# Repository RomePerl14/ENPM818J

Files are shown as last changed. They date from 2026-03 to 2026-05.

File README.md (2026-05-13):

# FINAL PROJECT OVERVIEW

For my final project submission, I used a PD controller and an ESP32 to control a brushless DC motor. This README contains the hardware used by the system, the system electronics and wiring, and the software to drive the system. By the end of this README, you should build and replicate the results exaclty from this final project! At least, that is my hope with this README :)

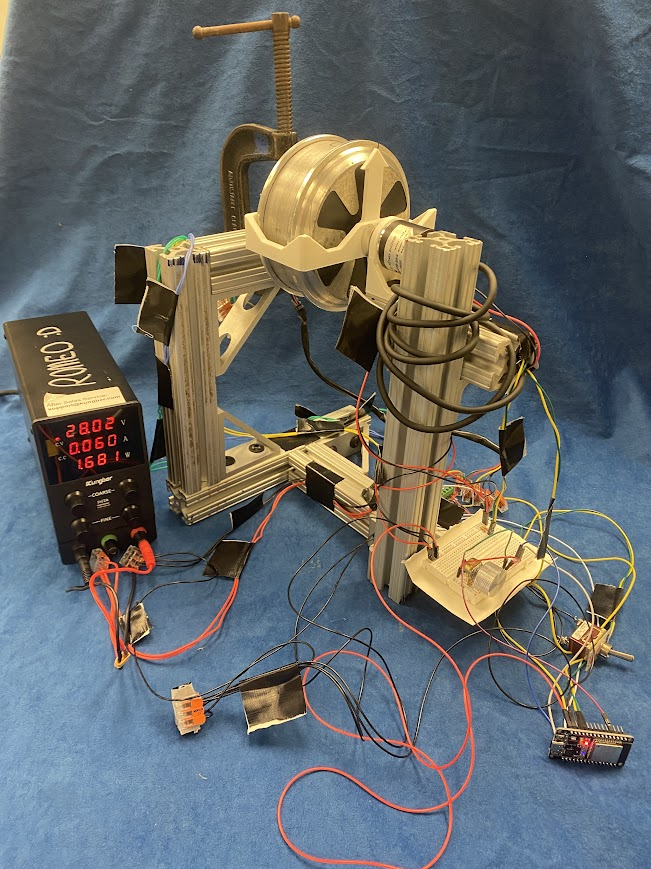
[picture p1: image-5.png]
 

## VIDEOS (click on images)
### ALL ENCOMPASSING VIDEO (I spliced everything into one video)
WATCH ME! (https://www.youtube.com/watch?v=Hu35tKas5SA)
### FINAL PRESENTATION VIDEO
IMAGE ALT TEXT HERE (https://www.youtube.com/watch?v=4x_1EzVbeUM)
### CODE OVERVIEW VIDEO
IMAGE ALT TEXT HERE (https://www.youtube.com/watch?v=HJQnwBiKr0g)
### CODE OVERVIEW WITH SYSTEM DEMO
IMAGE ALT TEXT HERE (https://www.youtube.com/watch?v=exr8jvf5Yu8)
### SYSTEM DEMO
IMAGE ALT TEXT HERE (https://www.youtube.com/watch?v=Gk0GASkIG9Y)

## Tools Needed:
- Wire strippers
- Dupont wire crimper
- Dupont wire connectors, or Arduino jumper wires (a LOT, see wiring diagram)
- Soldering tool
- Solder
- [1] large C-clamp
- 3/16 allen wrench (I think)

## Hardware Requirements
- [1] ESP32-WROOM-32: https://a.co/d/05TtJUjU
- [1] USB-C data cable
- [1] Hoverboard Motor: https://a.co/d/0681CQAJ (DO NOT BUY THIS - this is just an example of the motor. Any 3-Phase, 120 degree out-of-phase motor with an included hall effect sensor *should* work)
- [1] RioRand 350W 6-60V 3-Phase PWM DC Brushless Motor Speed Controller with Hall Sensor: https://a.co/d/0fNlEnNE
- [1] Any 28V (or more) power supply will work, measured no-load power was ~10 Watts 
- [n] 1515 8020 aluminum extrusion (see attached CAD for exact details and dimensions, though these are not hard requirements)
- [3] 15 series 8020 Tall Gusseted Inside Corner Bracket: https://8020.net/4336.html
- [3] 15 series 8020 Lite Transition Inside Corner Bracket: https://8020.net/4509.html
- [20] 15 series 8020 Bolt Assembly: https://8020.net/3320.html
- [1] Breadboard or equivalent way of connecting circuitry together (see circuit diagram below, or here [TODO - attach link])
- [1] One-turn analog potentiometer
- [2] 2.2k Ohm resistors
- [1] basic on/off switch
- [20] WAGO Lever-Nuts 3-Conductors varient (or more, less probably won't work without being annoying): https://a.co/d/0gCFwZCQ
- [1] Taiss/Incremental Rotary Quadrature Encoder, 600P/R: https://a.co/d/0cLU70xH
- 3D printer or ability to 3D print 3 components
- [1] goBilda 1309 Series Sonic Hub (6mm D-Bore): https://www.gobilda.com/1309-series-sonic-hub-6mm-d-bore/
- [3] M3 x 8mm
- [4] M4 x 20mm
- [2] M4 x 12mm

## Software Requirements
- ESP-IDF v2.1.0 (I used the VScode plugin and followed instructions on getting it working directly from Espressif): https://docs.espressif.com/projects/esp-idf/en/stable/esp32/get-started/index.html
- Visual Studio Code
- Windows 11 (?)

## Software Configuration
In your project configuration, specifically in ```sdkconfig```, you must change the following parameters:

```CONFIG_FREERTOS_HZ=100```

Change this too:

```CONFIG_FREERTOS_HZ=1000```

# SETTING UP THE HARDWARE
## Step 1: print the hardware
The system relies on three 3D prints to connect the motor and the encoder. The motor doesn't have any traditional mounting holes since it was original designed to spin a tire really fast, and the tire was built into the rotor. As such, we need to print an adapter to allow us to connect the motor and the encoder. We also need to print a mount for the encoder.

### MOTOR SIDE PRINTS
The two prints that are attached to the motor are the armature and direction arrow. You can find them here [TODO - ADD LINK]

<u>**Motor-To-Encoder Armatrure:**</u>

<img src="image-2.png" width="400"/> 

<img src="image-3.png" width="400"/> 

<u>**Direction Indicator Arm:**</u>

<img src="image-4.png" width="200"/> 

### ENCODER SIDE PRINTS
The only print needed for the encoder is it's mount, which you can find [here](FinalProj/STL/)

<u>**Encoder Mount:**</u>

<img src="image.png" width="300"/> 
<img src="image-1.png" width="300"/>

### 8020 MOTOR MOUNT
Because this is a little complex and also not necessarily required (another mounting method can be designed), see the CAD for more detail [TODO - ADD LINK]

[TODO - ADD PICTURES OF THE CAD]

# SETTING UP THE ELECTRONICS
Below is an electrical schematic of the system. You can utilize the WAGO connectors for most connections, however you will need jumper wires for connecting to the ESP32 and other peripherals. The general implementation is up to interpretation, however the exact wiring of the system used for this project is reflected in the wiring diagram!

[TODO -ADD PICTURE OF WIRING DIAGRAM]

# SETTING UP THE SOFTWARE
After installing Visual Studio Code, ESP-IDF, and the VSCode ESP-IDF extension, you can then clone this repository, or whatever means you want to get the ESP32 project code onto your own machine. Once it's on your machine and your project is configured, you should be able to build, flash, and monitor the code out-of-the-box! There are no external libraries utilized, just ESP32 libraries, C libraries, and FreeRTOS libraries (which should be downloaded with ESP-IDF).

## Software Overview
You will find all the code to run this project in one simply file: *`the_main_thingy.c`*. This File is located in the FinalProj/rotary_encoder/main/ folder. It's CMakeList.txt file (generated by ESP-IDF) is also in that file

There are three main tasks being run by the ESP32:
- The control task, running at 1000 Hz on CORE 1
    
- The potentiometer task, running at 100 Hz on CORE 0
    - Running it at 100 Hz allows the potentiometer to be sampled rather quickly and enable good tracking of the system
- The display task, running at 10 Hz on CORE 0
    - Because this is not a critical task, we run at an O.K. speed

### The Control Loop Task [```position_pid_task()```]
This task runs the PD control loop, and thats it! It reads the encoder counts from the onboard pulse counter, computes the command signal, and then writes a PWM value. The control loop itself is very standard:
- read() [```ctrl_loop_read(int *encoder_counts)```]
    - read the measurements from the incremental encoder, specifically read the output from ```pcnt_unit_get_count()```
- update() [```compute_position_pid_standard(float err, float prev_err, pid_gains gains, float freq)```]
    - Get the user command, and generate the control signal from the PD controller 
    - note that err, prev_err are computed in the task's while loop, not in the above function. pid_gains and frequency should technically be constants
- write() [```ctrl_loop_write(float *U)```]
    - Generate the PWM signal based on the PD controllers output, and write it to the PWM generator using ```ledc_set_duty()``` and ```ledc_update_duty()```

There is an additional update function called ```compute_position_pid_velocity(float err, float vel, pid_gains gains)``` which uses the velocity as a damping factor, rather than the change in error

#### Data Structures
There are two custom data structure implemented to ease function inputs, the ```pid_gains``` struct and the `pid_mode` enumerator. `pid_gains` stores the PID gains for the controller. The members of the struct Kp, Kd, and Ki are set before the beginning of the while loop in the task. `pid_mode` is used to switch between change in error PID or direct velocity PID

#### Interesting Things
To reduce the need to divide, many conversion factors which would require divison are pre-computed before the beginning of the while loop. In addition, rather than deriving the position measurements to get measured velocity using the common formula:

```(p(t) - p(t-1))/dt```

We use:

```(p(t) - p(t-1))*freq```

Since our control frequency is stable (or at least, should be thanks to FreeRTOS), we can say that our delta time is "constant" and 1/dt = 1/period = frequency. Thus, saving us the need to divide in order to get velocity. This is done a lot, where the inverse is computed ahead of time and then multiplied by, in an attempt to *not have to divide.*

We also used ```vTaskDelayUntil()``` rather than ```vTaskDelay()``` since we want our code to mandate a 1kHz frequency. Seemingly, the control loop computation is faster than 1 ms, allowing us to wait until we 1ms has passed before returning

Finally, we also store the the actual position, desired position (or commanded), the encoder counts, the error, and the control signal in global buffers labeled ```ACTUAL_POS```, ```ENCODER_COUNTS```, ```ERROR```, ```CONTROL_SIGNAL``` so that our display task can handle printing to the terminal, rather than the control loop.

We SHOULD filter the velocity signal using a low-pass filter (example from here: https://kiritchatterjee.wordpress.com/2014/11/10/a-simple-digital-low-pass-filter-in-c/) because it's WAY noisy! But I haven't implemented that yet. I should probably filter the potentiometer too!

### The Potentiometer Task [`read_potentiometer_task()`]
This is pretty much stripped directly from their example, as there was no point in fixing a broken clock if it's right twice a day, or something like that! You can find the ESP32 source code here: https://github.com/espressif/esp-idf/tree/v6.0.1/examples/peripherals/adc/continuous_read

### The Display Task [`display_control_data_task()`]
This task is very straight forward. Get the data from the buffers, and then print it to the console!

### PWM Generator
Its important to note that the PWM generator is generating a signal with a frequency of 20kHz. From online research (googling), 20kHz seemed to be a good PWM frequency to ensure good motor control. With this goal in mind, we needed to calculate the control duty resolution (see PWM generator below), and found that our maximum PWM command was 2047 bits, and our resolution was 1 bit, so we have  2047 different possible commands to send to the hardware.

## Final Takeaways
Many of the things implemented for this project were borrowed from other pioneers on the internet. Here are my sources:
- Motor driver wiring information: https://mad-ee.com/easy-inexpensive-hoverboard-motor-controller/
- ESP32 pinouts: https://lastminuteengineers.com/esp32-pinout-reference/
- ESP32-IDF examples (of which I used many): https://github.com/espressif/esp-idf/tree/v6.0.1/examples
    - potentiometer: https://github.com/espressif/esp-idf/tree/v6.0.1/examples/peripherals/adc/continuous_read
    - PWM generator: https://github.com/espressif/esp-idf/tree/v6.0.1/examples/peripherals/ledc/ledc_basic
    - Generic GPIO: https://github.com/espressif/esp-idf/tree/v6.0.1/examples/peripherals/gpio/generic_gpio
    - Encoder counter: https://github.com/espressif/esp-idf/tree/v6.0.1/examples/peripherals/pcnt/rotary_encoder
    - Duty Cycle and Precision calculations: https://documentation.espressif.com/esp32_technical_reference_manual_en.pdf#ledpwm, https://docs.espressif.com/projects/esp-idf/en/v4.3/esp32/api-reference/peripherals/ledc.html
    - PID control loop with a similar device: https://geekeeceebee.com/DCMotor%20Position%20Tracking.html
    - Task creation stuff: https://randomnerdtutorials.com/esp32-dual-core-arduino-ide/

Without the above documentation, this project (which I started on 5/8, and ended on 5/11... my parts didn't come in until 5/6!!) I would have NEVER been able to actually build this system, let alone get it running. But, I've gotten it running, and I'm quite proud of the little scamp. The poorly tuned, aggressive, spaghetti-like scamp. Hopefully if you are reading this, you may also one day be proud of your own little PID testbed, maybe even this very one!

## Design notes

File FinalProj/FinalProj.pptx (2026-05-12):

## Real-Time Position and Velocity Control of a Brushless DC Motor

Romeo Perlstein
ENPM818J Final Project

## Team

Romeo Perlstein:
- Aerospace Engineering Masters Student
- Likes space robots, human spaceflight, and human/robot collaboration in space

## Project Overview

Mission Statement:
Control the position of a hobby-grade brushless DC motor

## Requirements

Mission Level Requirements:
1. Fast control loop to implement basic PD controller
2. Position encoder to track live position of motor
3. Brushless DC motor
4. Brushless DC motor driver

## Requirements

Mission Level Requirements Reasonings:
1. PD controller needs to run at a relatively fast rate for good tracking
2. Need positional sensor readings in order to command position using PD controller
3. Need physical actuator to drive system, brushless DC motors are relatively challenging to work with compared to brushed DC motors and enable a more challenging project
4. Need a drive to convert command signals to phase current cycles (developing a custom one deemed out-of-scope)

## Requirements Cont’d

System Level Requirements:
1. Control loop that can run on the order of ~1kHz
2. Ability to read encoder pulses at frequency of ~10kHz
3. Ability to generate pulse-width-modulated (PWM) signal at frequency of roughly ~20kHz
4. Ability to send digital outputs at a fast rate (~1kHz)
5. Control input circuit (a.k.a potentiometer) for position commands

## Requirements Cont’d

System Level Requirements Reasoning:
1. Position PID control of motors needs to run at frequencies on the order of kHz or faster for stable and smooth control
2. High-resolution encoders generate pulses faster than typical while loops or interrupt service routines can handle
3. High frequency PWM signals enable smooth motor motion
4. Digital output for direction has to change at the same rate of the control loop
5. User input to demonstrate motor control

## Final System

## Final System (labeled)

## Core Components

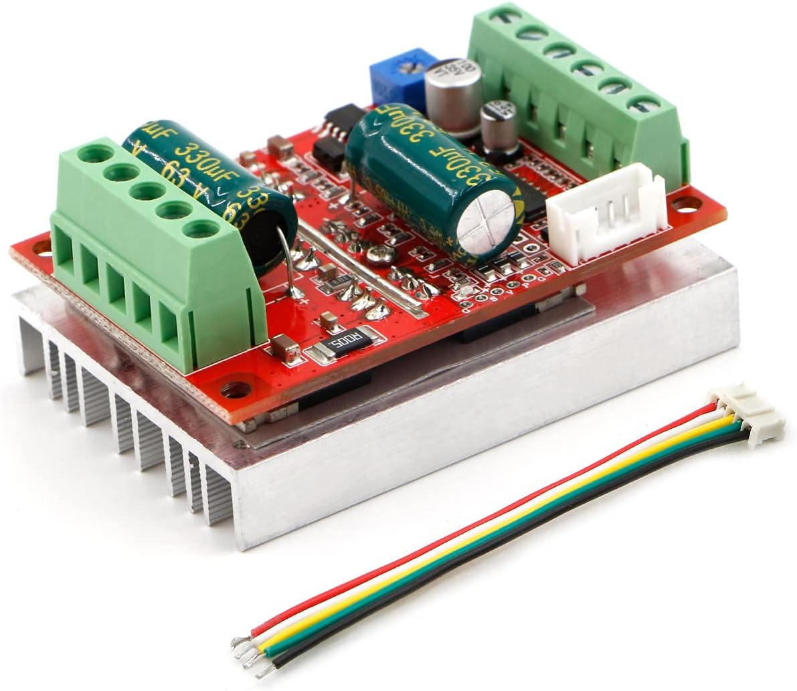
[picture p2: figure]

- RioRand 3-Phase Brushless DC motor driver with PWM input
- Hoverboard motor
- 1515 80/20 extrusion
- ESP32 WROOM
- Quadrature Encoder

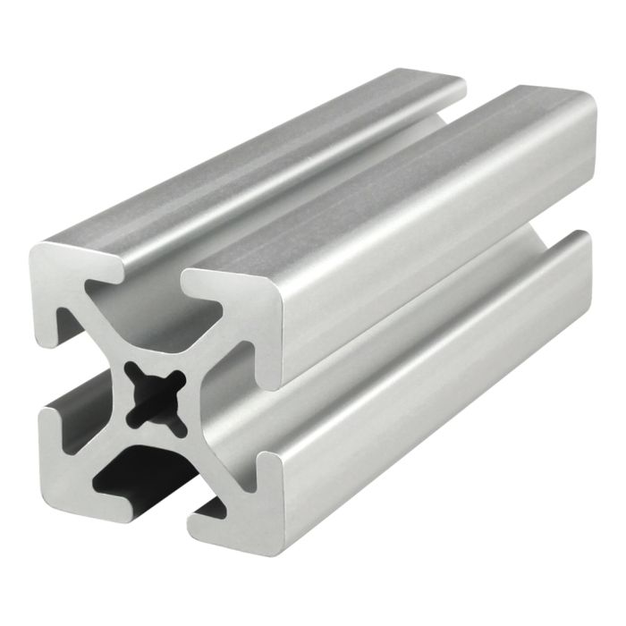
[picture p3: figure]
1515-S | 1.50” X 1.50” Smooth Surface T-Slotted Profile - Four Open T-Slots
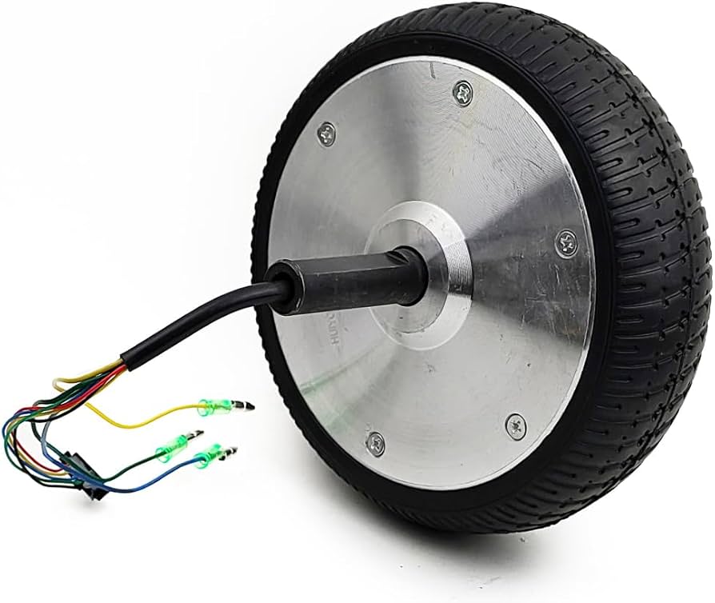
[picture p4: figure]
Amazon.com: 6.5 Inch Self Balancing Scooter Motor Wheel with Tire Self Balance Unicycle Hover Board Motor Replacement : Sports & Outdoors
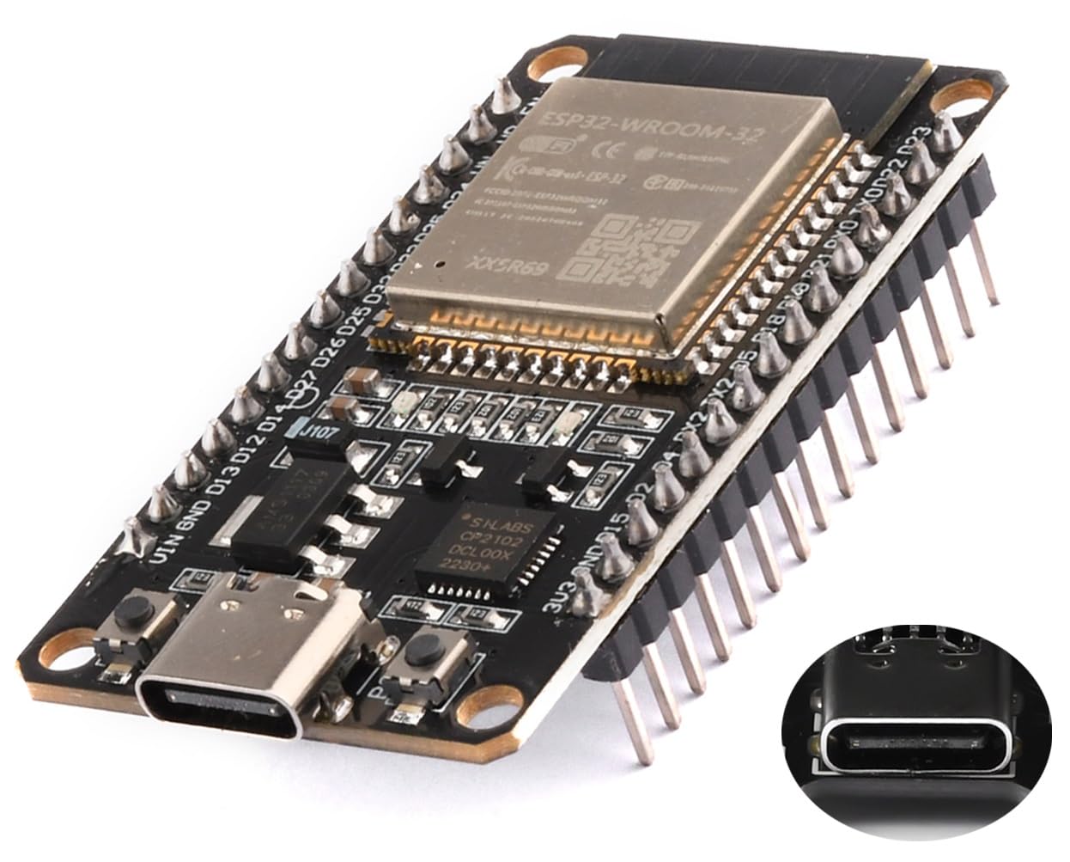
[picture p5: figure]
Amazon.com: ESP32 Type-C Module ESP32 30PIN NodeMCU Development Board ESP32- WROOM-32 2.4 GHz WLAN CP-2102 : Electronics
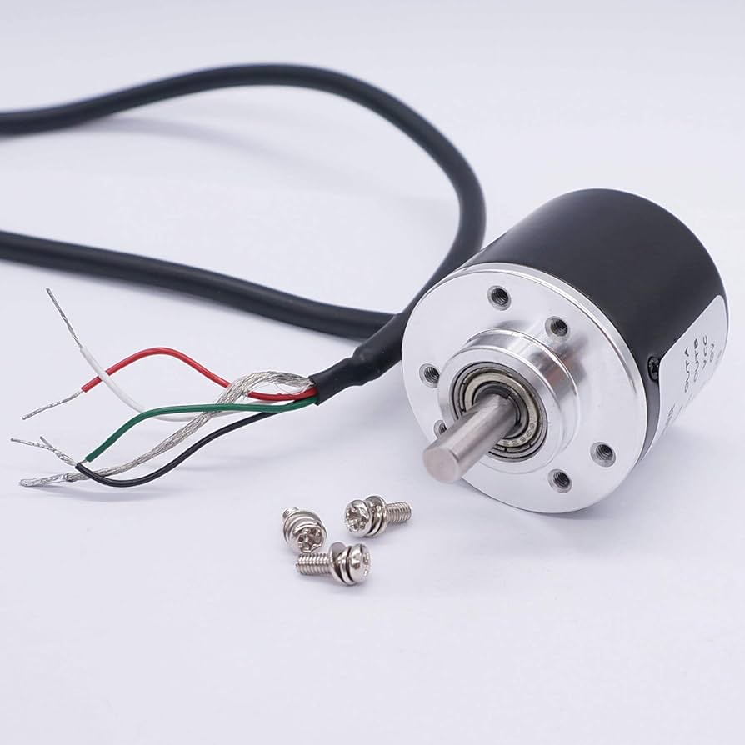
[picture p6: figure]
Amazon.com: Taiss/AB 2 phase Incremental Rotary Encoder 360P/R DC 5-24v Wide Voltage Power Supply 6mm Shaft 360P/R : Industrial & Scientific

## Additional Components

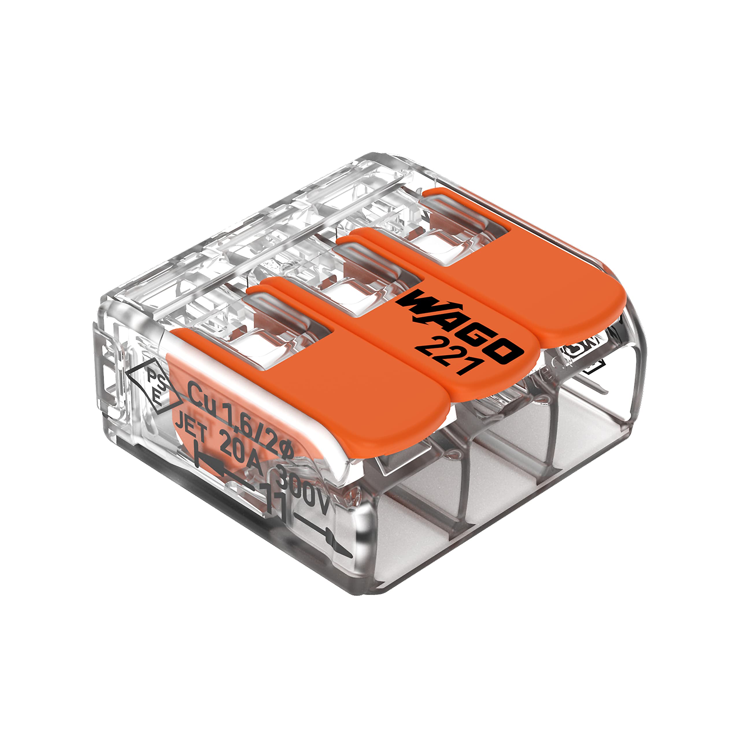
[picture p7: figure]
Amazon.com: 221-413 | WAGO Lever-Nuts® Splicing Connector | for Solid and Stranded Conductors | 3-Conductor with Operating levers | 24-12 AWG | Transparent housing | [Box of 50 Pieces] : Industrial & Scientific

- WAGO lever-lock connectors
- Breadboard
- 30V-10A power supply
- Enable/disable switch
- Potentiometer
- C-clamp

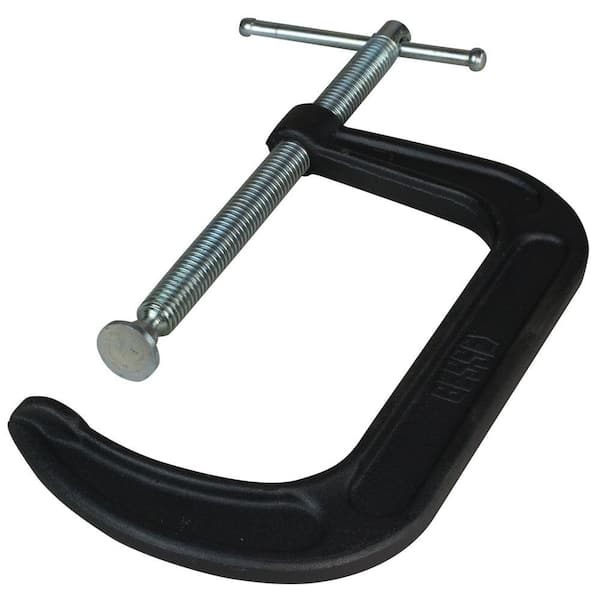
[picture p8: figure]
BESSEY CM Series 6 in. Capacity Drop Forged C-Clamp with 3-1/2 in. Throat Depth CM60 - The Home Depot
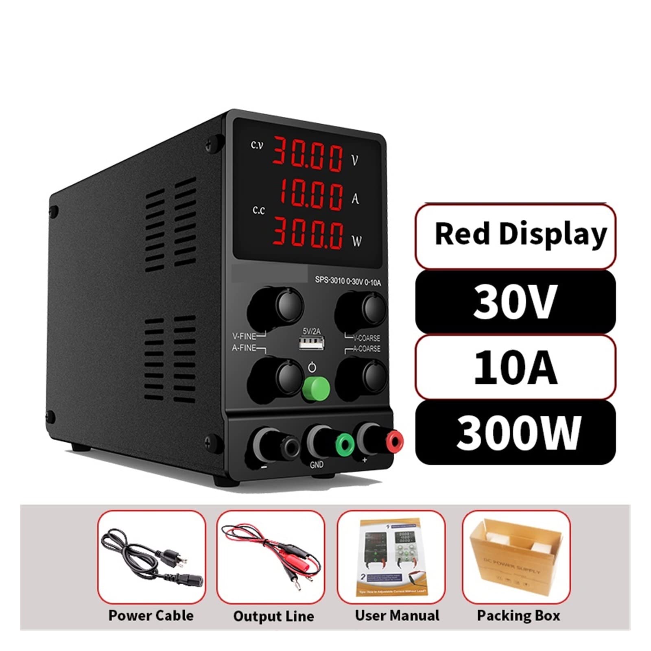
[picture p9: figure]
Amazon.com: PACUM Variable DC Power Supply Adjustable DC Power Supply 30V 10A 60V5A Lab Bench Power Supply Laboratory Stabilized Power Supply Voltage Regulator Switch Power Supply Adjustable(Red Display 30V10A) : Industrial &

## Operational Parameters

- PWM frequency: 20kHz
- PID Control loop: 1kHz
- PD controller gains (did not spend a lot of time tuning)
  - Kp = 0.6
  - Kd = 0.025
- User control input frequency: 100Hz
- Data logging frequency: 10Hz

## Software Overview

- Main Control task runs on ESP32 CORE 1 with priority 1
- User Input control task runs on ESP32 CORE 0 with priority 1
- Data logging loop task runs on ESP32 CORE 0 with priority 2
Data is shared between cores and tasks using global buffers
See video overview for more in-depth information

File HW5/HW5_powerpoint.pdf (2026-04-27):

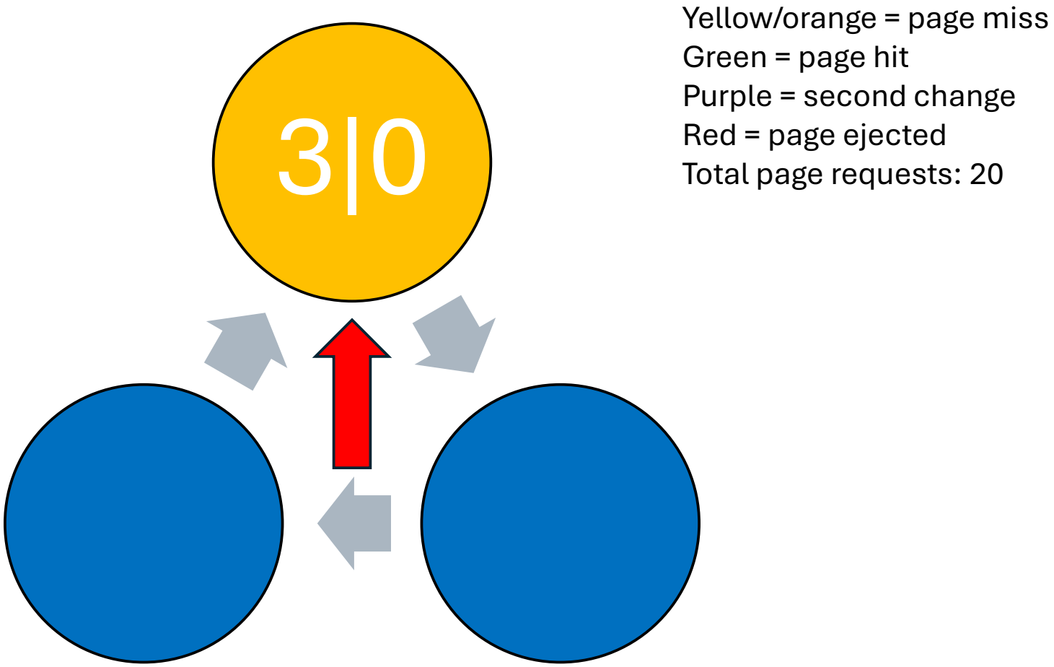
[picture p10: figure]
Yellow/orange = page miss Green = page hit Purple = second change Red = page ejected Total page requests: 20

i =1

KEY:
page_number | reference_number

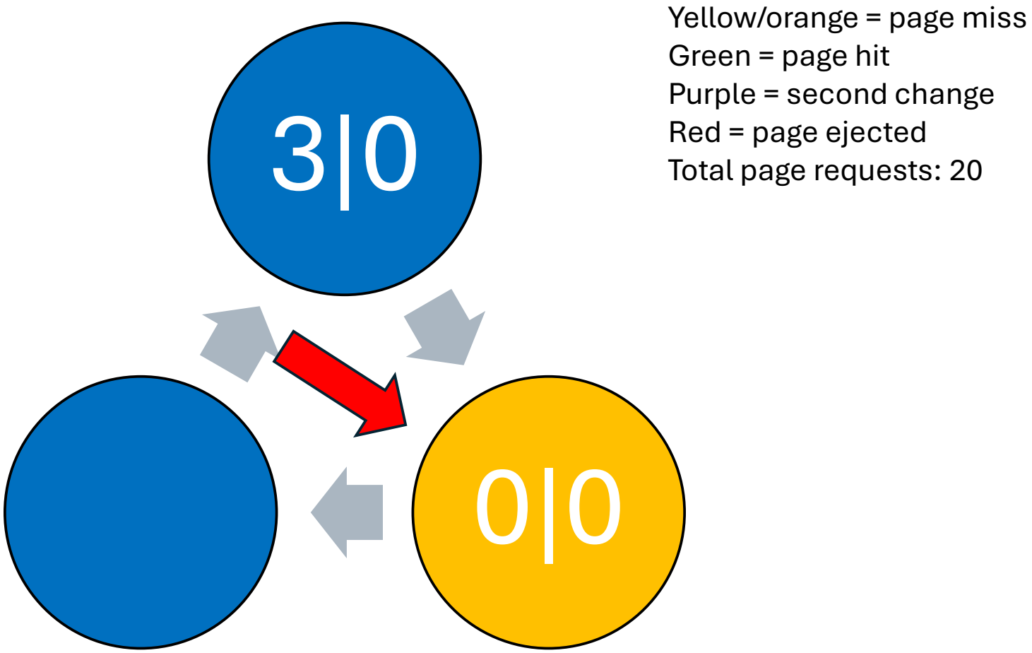
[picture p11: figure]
Yellow/orange = page miss Green = page hit Purple = second change Red = page ejected Total page requests: 20

i =2

page_number | reference_number

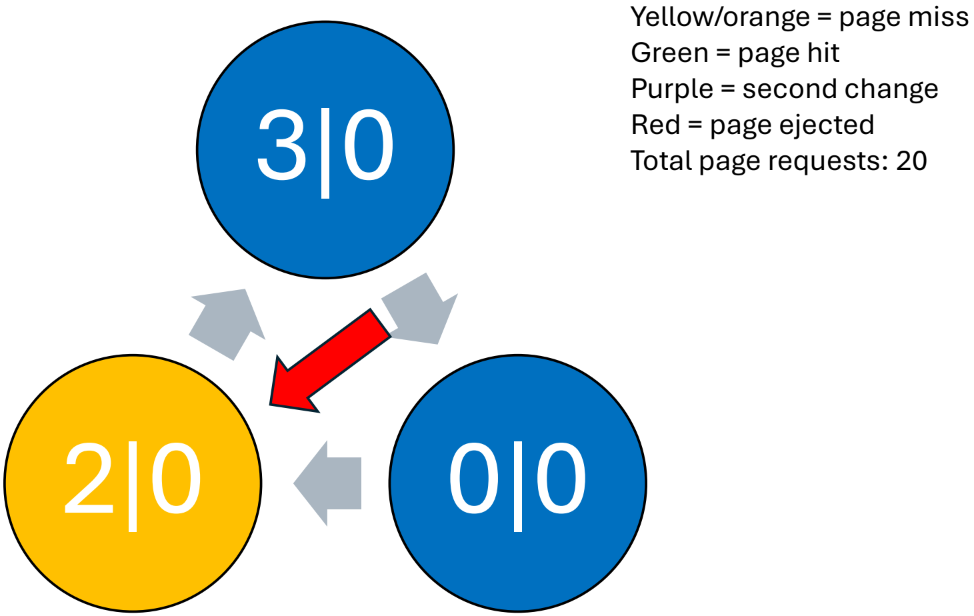
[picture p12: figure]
Yellow/orange = page miss Green = page hit Purple = second change Red = page ejected Total page requests: 20

i =3

page_number | reference_number

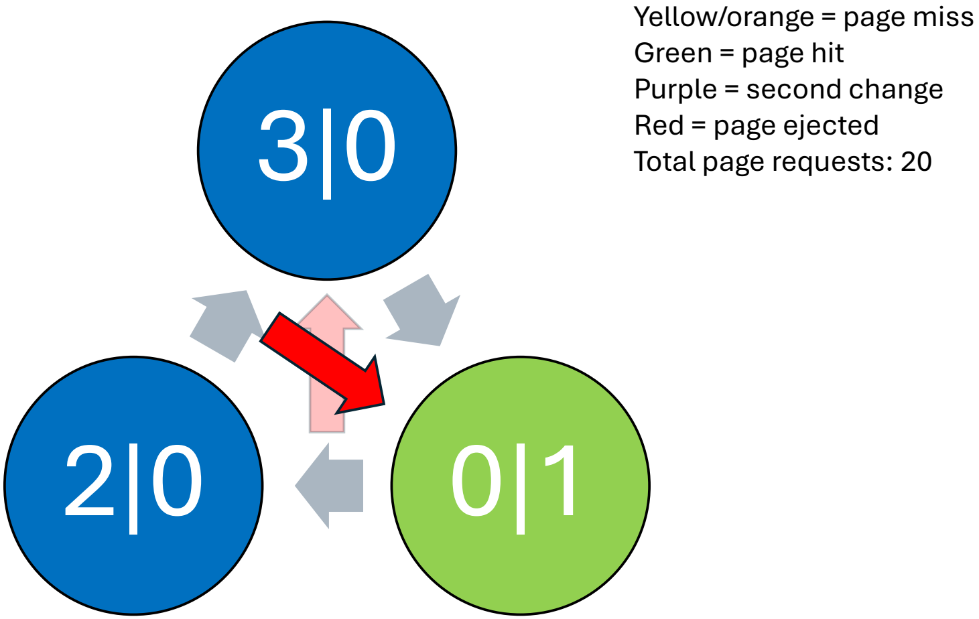
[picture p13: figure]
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

i =4

page_number | reference_number

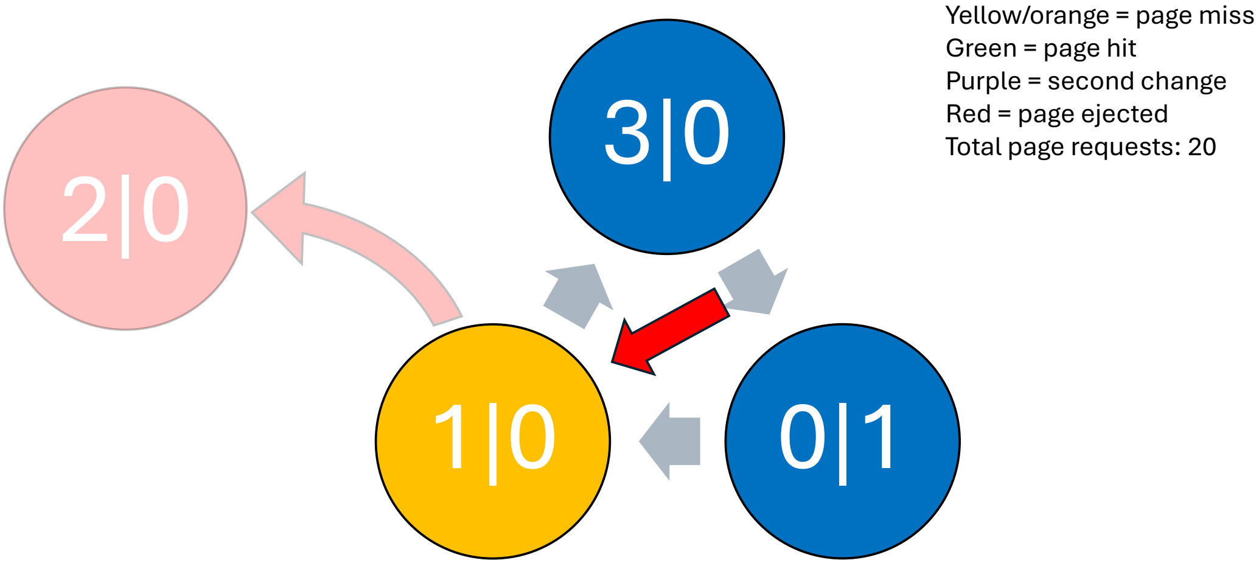
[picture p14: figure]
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

i =5

page_number | reference_number

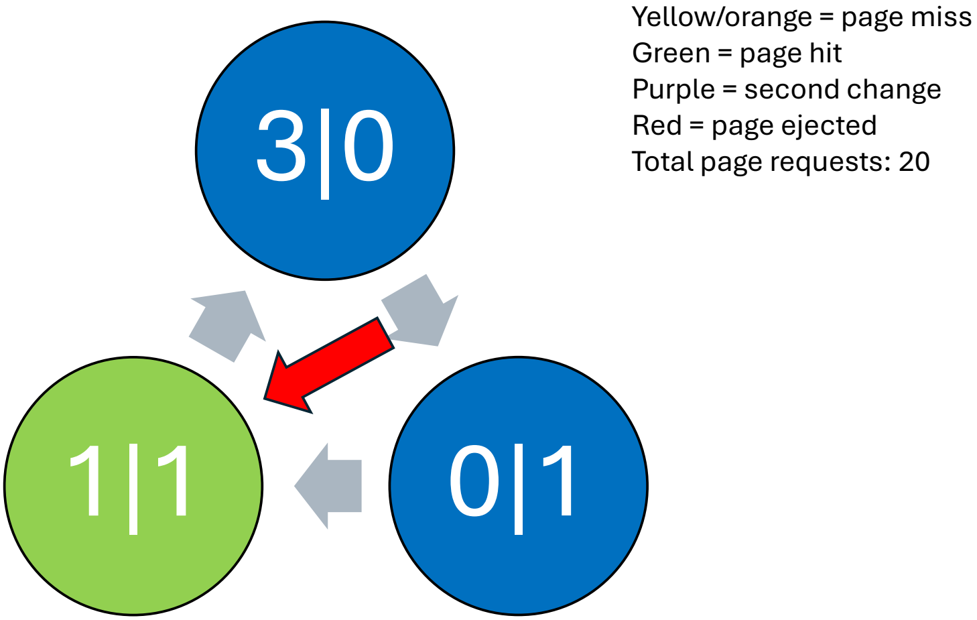
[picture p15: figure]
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

i =6

page_number | reference_number

i =7

page_number | reference_number

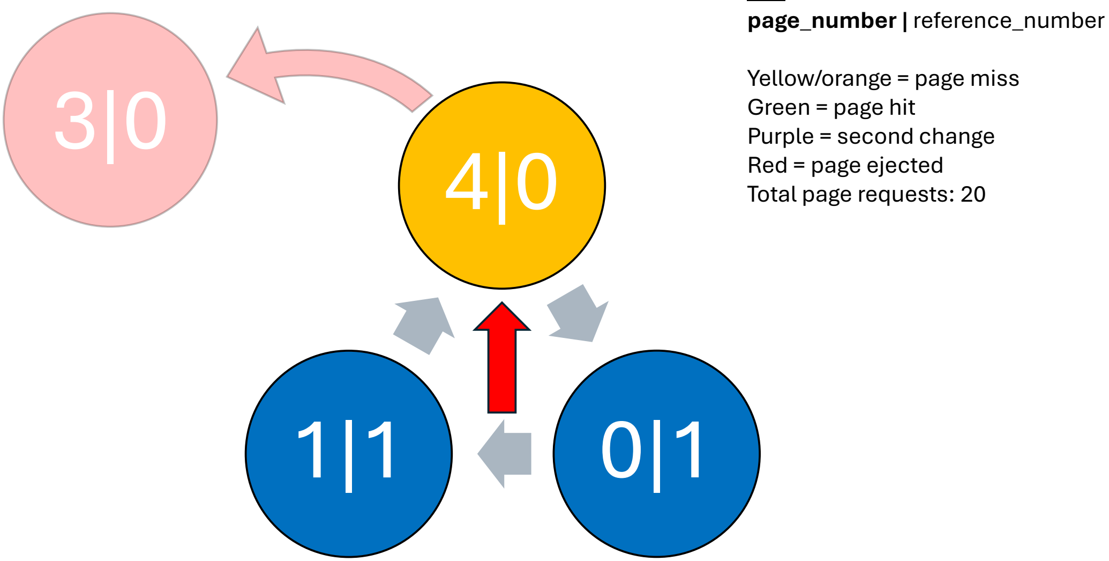
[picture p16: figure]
page_number | reference_number; Yellow/orange = page miss Green = page hit Purple = second change Red = page ejected Total page requests: 20

i =8

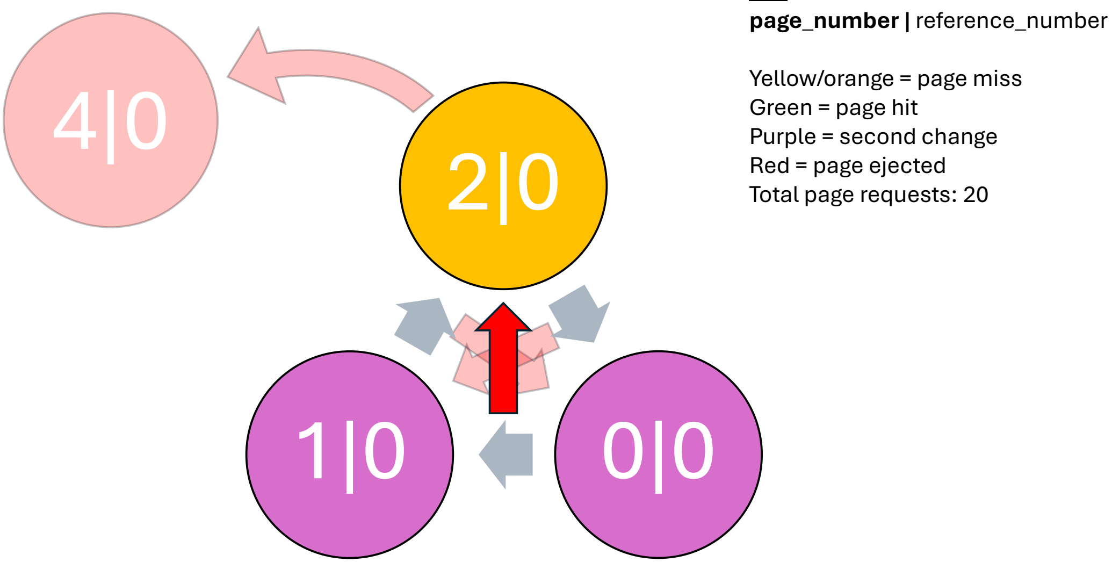
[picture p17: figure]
page_number | reference_number; Yellow/orange = page miss Green = page hit Purple = second change Red = page ejected Total page requests: 20

i =9

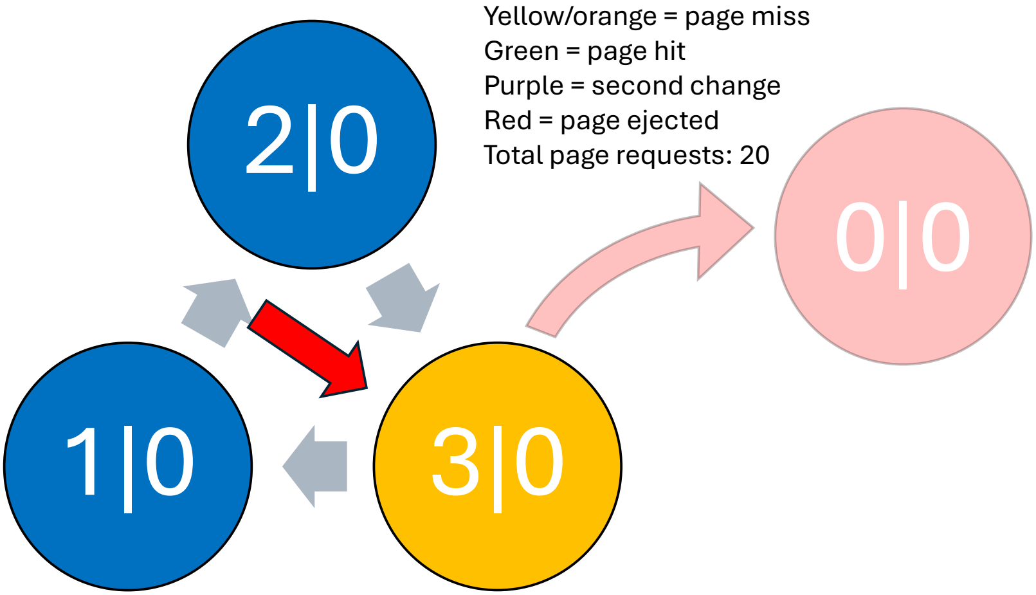
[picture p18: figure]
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

i =

10

page_number | reference_number

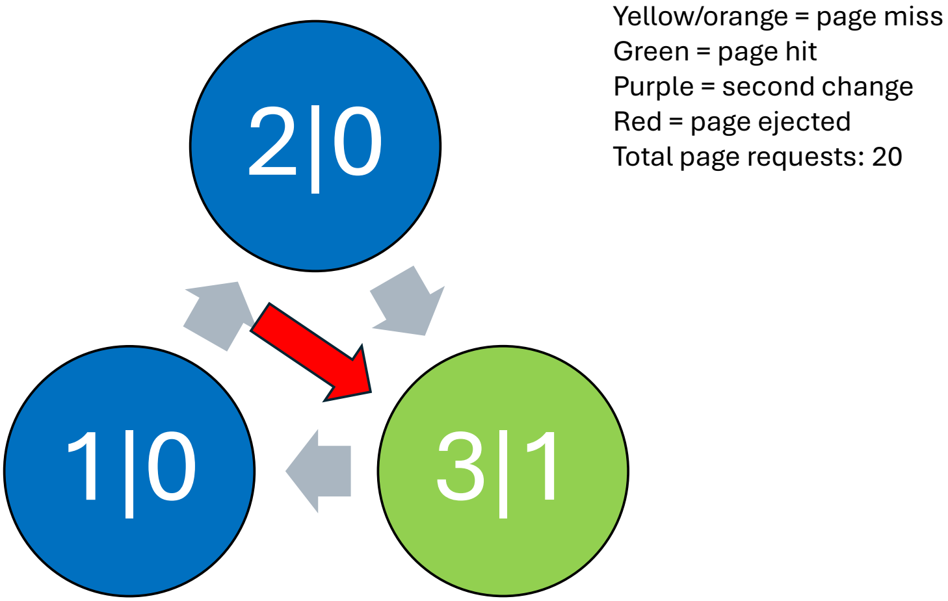
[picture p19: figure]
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

i =11

page_number | reference_number

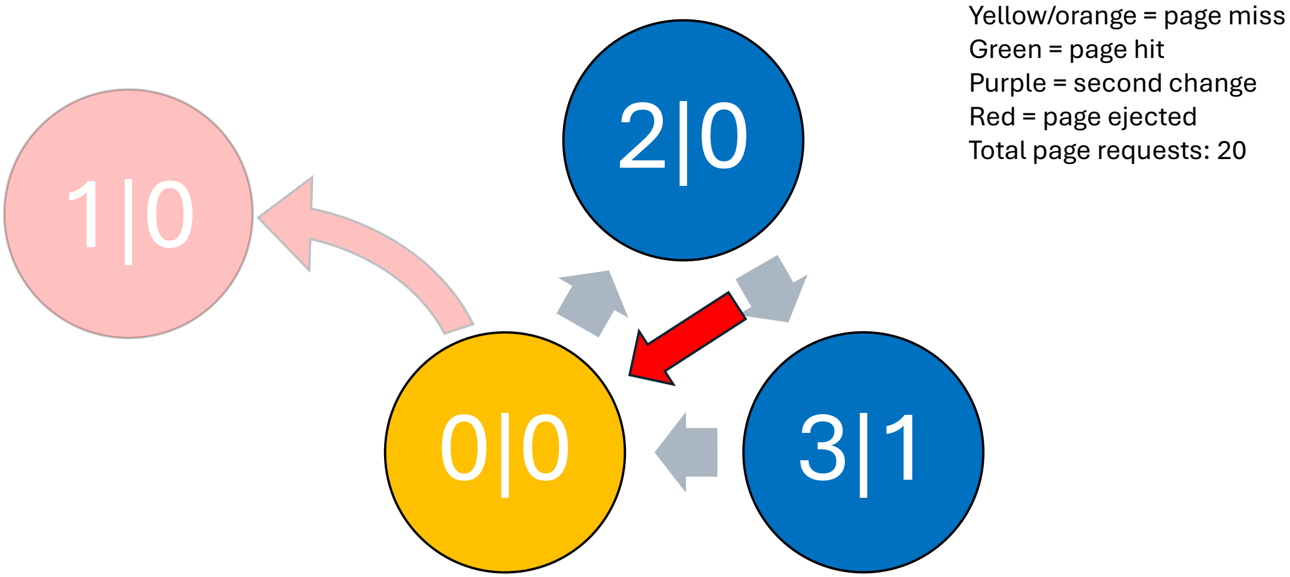
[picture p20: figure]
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

i =

12

page_number | reference_number

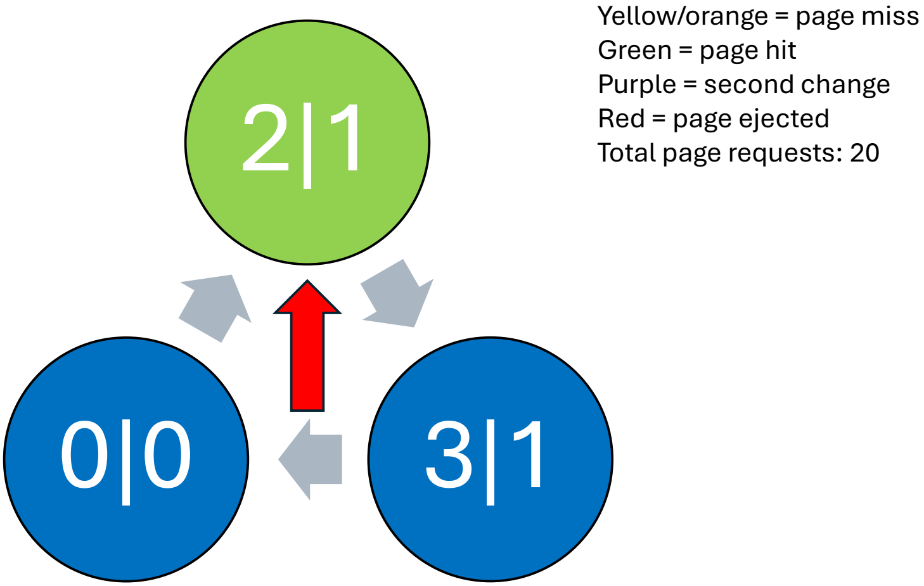
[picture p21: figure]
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

i =13

page_number | reference_number

i =14

page_number | reference_number

i =15

page_number | reference_number

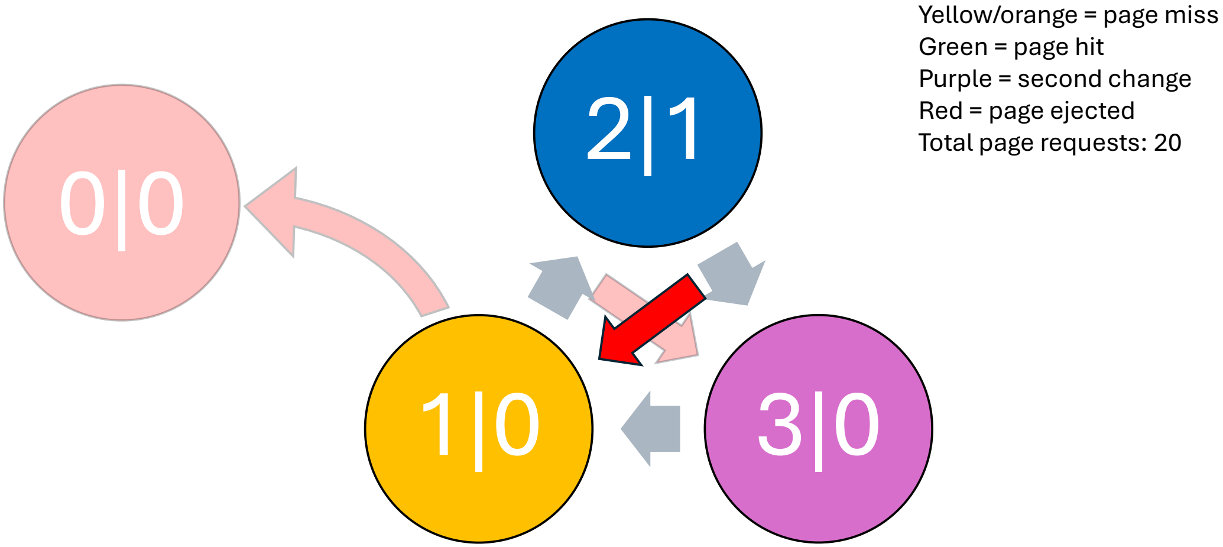
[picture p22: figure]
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

i =

16

page_number | reference_number

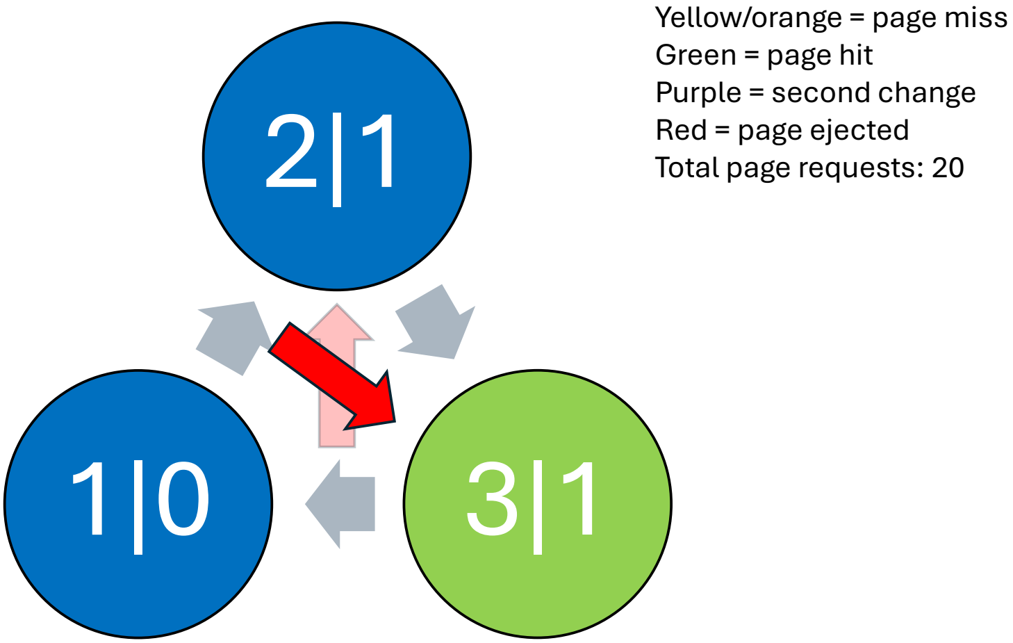
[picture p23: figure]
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

i =17

page_number | reference_number

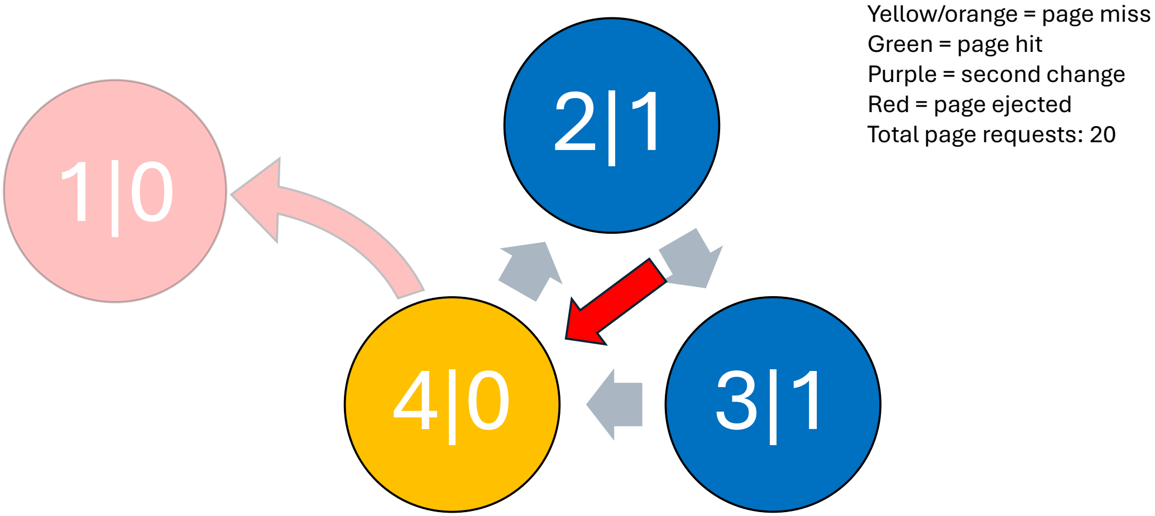
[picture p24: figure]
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

i =

18

page_number | reference_number

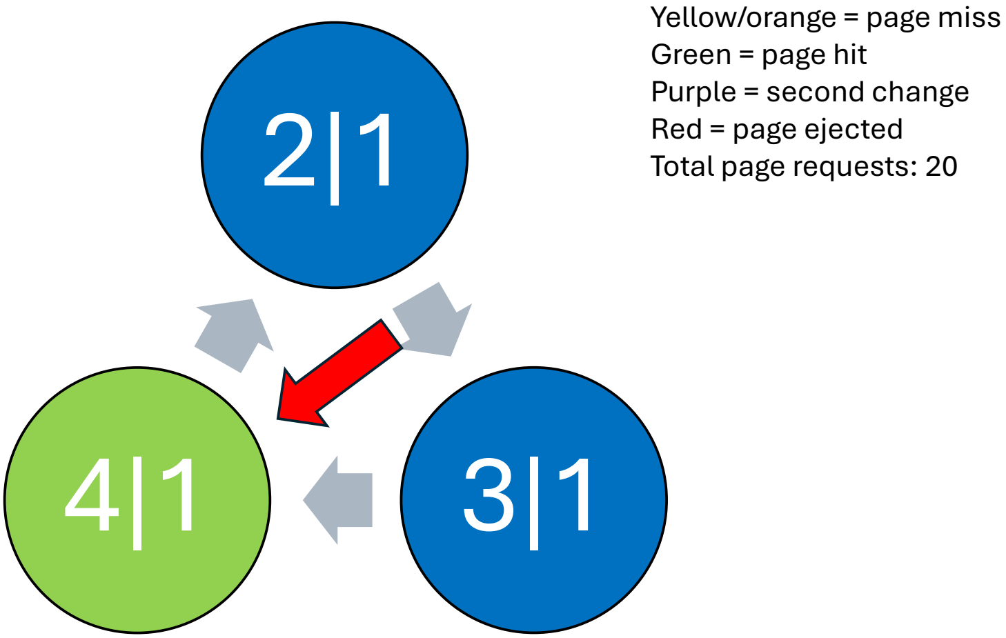
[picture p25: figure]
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

i =19

page_number | reference_number

i =20

page_number | reference_number

3|1 | 0|1 | 2|1 | 0|2 | 0|2 | 1|2 | 1|3 | 1|3 | 1|3 | 1|3 | 1|3 | 0|3 | 0|3 | 0|3 | 2|3 | 1|4 | 1|4 | 1|4 | 1|4 | 1|4
| 3|1 | 0|1 | 2|1 | 2|1 | 0|2 | 0|2 | 0|2 | 0|2 | 0|2 | 3|2 | 1|3 | 1|3 | 1|3 | 0|3 | 2|3 | 2|3 | 2|3 | 2|3 | 4|3
| | 3|1 | 3|1 | 1|1 | 2|1 | 2|1 | 4|1 | 2|1 | 3|1 | 0|2 | 3|2 | 2|1 | 2|2 | 1|3 | 0|3 | 3|1 | 4|1 | 4|2 | 2|3
page_number | reference_number

Yellow = page miss
Green = page hit
Total page requests: 20

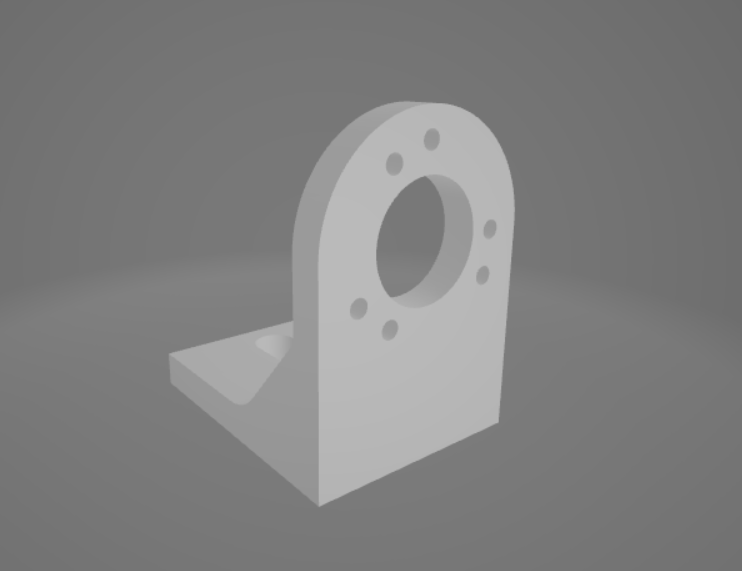
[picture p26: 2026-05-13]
image.png

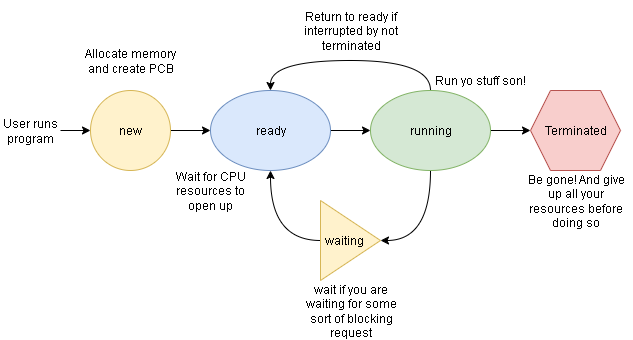
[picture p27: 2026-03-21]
Midterm/process_state_diagram.png

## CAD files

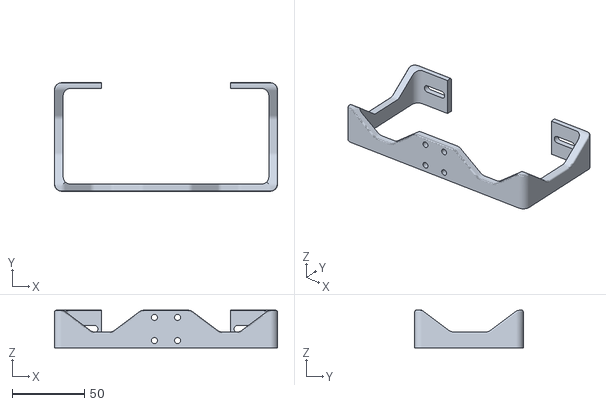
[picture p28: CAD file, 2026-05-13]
FinalProj/STL/armature.stl
154.0 x 75.0 x 26.0

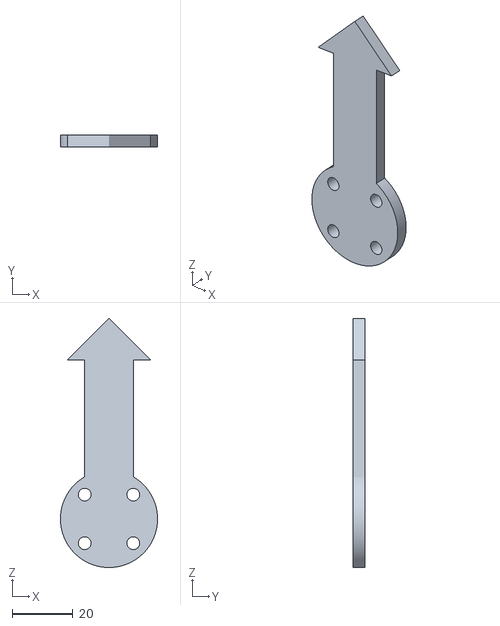
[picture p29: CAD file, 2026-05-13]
FinalProj/STL/arm.stl
32.0 x 4.00 x 82.0

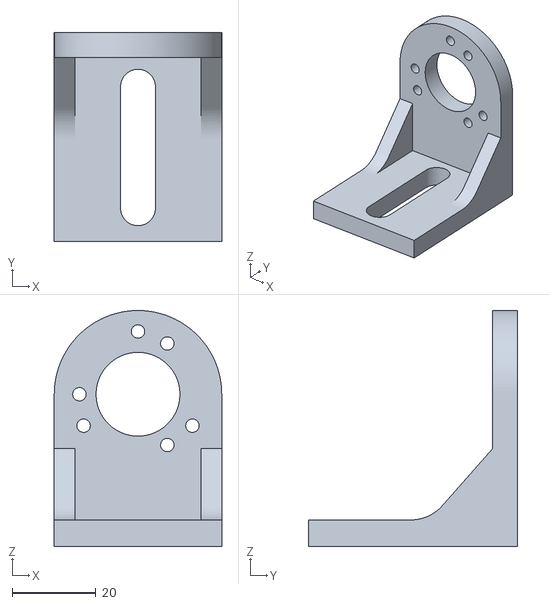
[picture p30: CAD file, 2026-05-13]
FinalProj/STL/encoder_mount.stl
40.0 x 50.0 x 56.3

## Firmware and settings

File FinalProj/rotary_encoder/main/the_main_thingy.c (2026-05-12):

/* ****************************************************************
 * (c) Copyright 2025                                             *
 * Romeo Perlstein                                                *
 * ENPM818J - Real Time Operating Systems                         *
 * FINAL PROJECT - THE MAIN THINGY                                *
 * College Park, MD 20742                                         *
 * https://terpconnect.umd.edu/~romeperl/                         *
 ******************************************************************/

// C LIBRARIES
#include <stdio.h>
#include <stdlib.h>
#include <math.h>

// ESP32 LIBRARIES
#include "sdkconfig.h"
#include "esp_log.h"
#include "esp_sleep.h"
#include "esp_err.h"
#include "esp_adc/adc_continuous.h"
#include "driver/pulse_cnt.h"
#include "driver/gpio.h"
#include "driver/ledc.h"

// FreeRTOS LIBRARIES
#include "freertos/FreeRTOS.h"
#include "freertos/task.h"
#include "freertos/queue.h" // unused, but keeping until we're done
#include "freertos/semphr.h"

//-------- Debug setup
static const char *TAG_position_PID = "[Position Ctrl]";
// static const char *TAG_velocity_PID = "[Velocity Ctrl]";
static const char *TAG_main = "[Main]";
static const char *TAG_pot = "[Potentiometer]";
static const char *TAG_display = "[DISPLAY]";

//-------- CONSTANTS
#define PI 3.14159265359

//-------- GPIO PIN SETTINGS
#define LEDC_OUTPUT_IO 2 // Define the PWM pin
#define DIRECTION_PIN 4
#define ENABLE_PIN 16
#define BRAKE_PIN 17
#define ENCODER_A_PIN 12
#define ENCODER_B_PIN 14
#define GPIO_OUTPUT_PINS ((1ULL<<DIRECTION_PIN) | (1ULL<<ENABLE_PIN) | (1ULL<<BRAKE_PIN))

//-------- PWM LEDC setup
#define LEDC_TIMER              LEDC_TIMER_0
#define LEDC_MODE               LEDC_HIGH_SPEED_MODE
#define LEDC_CHANNEL            LEDC_CHANNEL_0
#define LEDC_DUTY_RES           LEDC_TIMER_11_BIT // Set duty resolution to 11 bits (calculated maximum duty cycle)
uint16_t ledc_duty_ctrl_loop    = 2047;
#define LEDC_CLK_SRC            LEDC_APB_CLK // want to use the APB (80 MHz) clock!
#define LEDC_FREQUENCY          20000 // Frequency in Hertz. Set frequency at 20 kHz

//-------- Potentiometer setup
#define EXAMPLE_ADC_UNIT                    ADC_UNIT_1
#define EXAMPLE_ADC_CONV_MODE               ADC_CONV_SINGLE_UNIT_1
#define EXAMPLE_ADC_ATTEN                   ADC_ATTEN_DB_12
#define EXAMPLE_ADC_BIT_WIDTH               SOC_ADC_DIGI_MAX_BITWIDTH
#define EXAMPLE_READ_LEN                    256
static adc_channel_t channel[] = {ADC_CHANNEL_6};

//-------- CONTROL LOOP PARAMETERS
float Umax = 28; // Because out control loop outputs voltages (I think), our max operating voltage is 28V
float Umax_inv; // inverse of Umax to avoid dividing in the loop

// TODO overflow value for the encoder - used in conjunction with overlow catch ability in the PCNT
int EXAMPLE_PCNT_HIGH_LIMIT = 24000; // can do 10 positive turns starting from 0 without overflowing
int EXAMPLE_PCNT_LOW_LIMIT = -24000; // can do 10 negative turns starting from 0 without overflowing
int encoder_counts_per_rev = 2400; // encoder counts per revolution. Since encoder is 600 P/R, the quadrature encoder counts are 4x the P/R

// control loop frequencies, to be used by each task
float ctrl_freq_position = 1000; // Hz
// float ctrl_freq_velocity = 500; // Hz

// PID struct
typedef struct 
{
    float Kp;
    float Kd;
    float Ki;
} pid_gains;

// PID type
typedef enum {
  STANDARD,
  VELOCITY,
} pid_mode;
pid_mode mode = VELOCITY;

//-------- POSITION LOOP PARAMETERS
float Kp_pos = 5;
float Kd_pos = 0.025;
float Ki_pos = 0;
float Beta = 0.9; // velocity filtering

// //-------- VELOCITY LOOP PARAMETERS
// float Kp_vel = 10;
// float Kd_vel = 0;
// float Ki_vel = 0;

// channel definitions for PCNT counter - global variables because the position and velocity tasks are sharing the resources and need to claim them when running
pcnt_unit_config_t unit_config = {};
pcnt_unit_handle_t pcnt_unit;
pcnt_glitch_filter_config_t filter_config = {};
pcnt_chan_config_t chan_a_config = {};
pcnt_chan_config_t chan_b_config = {};
pcnt_channel_handle_t pcnt_chan_a;
pcnt_channel_handle_t pcnt_chan_b;

// TASK HANDLES
TaskHandle_t control_loop_task;
TaskHandle_t read_pot_task;
TaskHandle_t display_data_task;

// DATA BUFFERS
SemaphoreHandle_t xMutex;
float COMMAND_POS = 0.0;
int POT_POSITION = 0;
float CONTROL_SIGNAL = 0.0;
int ENCODER_COUNTS = 0.0;
float ACTUAL_POS = 0.0;
float ERROR = 0.0;

// functionalizing to reduce clutter, but this does nothing of importance
void setup_pcnt_stuff()
{
    // copy the setup from the ESP32 example
    ESP_LOGI(TAG_main, "[%i] install pcnt unit", 0);
    unit_config.high_limit = EXAMPLE_PCNT_HIGH_LIMIT;
    unit_config.low_limit = EXAMPLE_PCNT_LOW_LIMIT;

    pcnt_unit = NULL;
    ESP_ERROR_CHECK(pcnt_new_unit(&unit_config, &pcnt_unit));

    ESP_LOGI(TAG_main, "[%i] set glitch filter", 0);
    filter_config.max_glitch_ns = 1000;
    ESP_ERROR_CHECK(pcnt_unit_set_glitch_filter(pcnt_unit, &filter_config));

    ESP_LOGI(TAG_main, "[%i] install pcnt channels", 0);
    chan_a_config.edge_gpio_num = ENCODER_A_PIN;
    chan_a_config.level_gpio_num = ENCODER_B_PIN;
    pcnt_chan_a = NULL;
    ESP_ERROR_CHECK(pcnt_new_channel(pcnt_unit, &chan_a_config, &pcnt_chan_a));

    chan_b_config.edge_gpio_num = ENCODER_B_PIN;
    chan_b_config.level_gpio_num = ENCODER_A_PIN;
    pcnt_chan_b = NULL;
    ESP_ERROR_CHECK(pcnt_new_channel(pcnt_unit, &chan_b_config, &pcnt_chan_b));

    ESP_LOGI(TAG_main, "[%i] set edge and level actions for pcnt channels", 0);
    ESP_ERROR_CHECK(pcnt_channel_set_edge_action(pcnt_chan_a, PCNT_CHANNEL_EDGE_ACTION_DECREASE, PCNT_CHANNEL_EDGE_ACTION_INCREASE));
    ESP_ERROR_CHECK(pcnt_channel_set_level_action(pcnt_chan_a, PCNT_CHANNEL_LEVEL_ACTION_KEEP, PCNT_CHANNEL_LEVEL_ACTION_INVERSE));
    ESP_ERROR_CHECK(pcnt_channel_set_edge_action(pcnt_chan_b, PCNT_CHANNEL_EDGE_ACTION_INCREASE, PCNT_CHANNEL_EDGE_ACTION_DECREASE));
    ESP_ERROR_CHECK(pcnt_channel_set_level_action(pcnt_chan_b, PCNT_CHANNEL_LEVEL_ACTION_KEEP, PCNT_CHANNEL_LEVEL_ACTION_INVERSE));

    ESP_LOGI(TAG_main, "[%i] enable pcnt unit", 0);
    ESP_ERROR_CHECK(pcnt_unit_enable(pcnt_unit));
    ESP_LOGI(TAG_main, "[%i] clear pcnt unit", 0);
    ESP_ERROR_CHECK(pcnt_unit_clear_count(pcnt_unit));
    ESP_LOGI(TAG_main, "[%i] start pcnt unit", 0);
    ESP_ERROR_CHECK(pcnt_unit_start(pcnt_unit));
}

void setup_gpio_stuff()
{
    //zero-initialize the config structure.
    gpio_config_t io_conf = {};
    //disable interrupt
    io_conf.intr_type = GPIO_INTR_DISABLE;
    //set as output mode
    io_conf.mode = GPIO_MODE_OUTPUT;
    //bit mask of the pins that you want to set
    io_conf.pin_bit_mask = GPIO_OUTPUT_PINS;
    //disable pull-down mode
    io_conf.pull_down_en = GPIO_PULLDOWN_DISABLE;
    //disable pull-up mode
    io_conf.pull_up_en = GPIO_PULLUP_DISABLE;
    //configure GPIO with the given settings
    gpio_config(&io_conf);
}

static void setup_ledc_stuff(void)
{
    // Prepare and then apply the LEDC PWM timer configuration
    ledc_timer_config_t ledc_timer = {
        .speed_mode       = LEDC_MODE,
        .duty_resolution  = LEDC_DUTY_RES,
        .timer_num        = LEDC_TIMER,
        .freq_hz          = LEDC_FREQUENCY,  // Set output frequency at 20 kHz
        .clk_cfg          = LEDC_CLK_SRC,
    };
    ESP_ERROR_CHECK(ledc_timer_config(&ledc_timer));

    // Prepare and then apply the LEDC PWM channel configuration
    ledc_channel_config_t ledc_channel = {
        .speed_mode     = LEDC_MODE,
        .channel        = LEDC_CHANNEL,
        .timer_sel      = LEDC_TIMER,
        .gpio_num       = LEDC_OUTPUT_IO,
        .duty           = 0, // Set duty to 0%
        .hpoint         = 0,
    };
    ESP_ERROR_CHECK(ledc_channel_config(&ledc_channel));
}

//-------- CONTROL LOOP FUNCTIONS
void ctrl_loop_read(int *encoder_counts_)
{
    // just get the encoder counts and pass them by reference
    ESP_ERROR_CHECK(pcnt_unit_get_count(pcnt_unit, encoder_counts_));
}

// control loop implementation borrow from: https://geekeeceebee.com/DCMotor%20Position%20Tracking.html
void ctrl_loop_write(float *U_)
{
    // enforce that our control input is within bounds
    if (*U_ > Umax)
    {
        *U_ = Umax;
    }
    else if (*U_ < -Umax)
    {
        *U_ = -Umax;
    }

    // generate the PWM signal based on the duty count and the current control signal
    int cycle = (int)((ledc_duty_ctrl_loop) * fabsf(*U_) * Umax_inv);
    if(cycle > (ledc_duty_ctrl_loop)) // should never be the case, but lets check anyway
    {
        cycle = (ledc_duty_ctrl_loop);
    }

    if(*U_ < 0)
    {
        // set the direction pin LOW 
        // Low is negative! so this should make sense
        gpio_set_level(DIRECTION_PIN, 0);
    }
    else if(*U_ >= 0)
    {
        // set the direction pin HIGH
        // high is positive! so this is good
        gpio_set_level(DIRECTION_PIN, 1);
    }
    //
    // update the PWM generator, and then write it
    ESP_ERROR_CHECK(ledc_set_duty(LEDC_MODE, LEDC_CHANNEL, cycle));
    ESP_ERROR_CHECK(ledc_update_duty(LEDC_MODE, LEDC_CHANNEL));
}

// we're just gonna do a PD loop for right now
// this function can be used for either position control or velocity control, how the output "u" is used just changes
float compute_position_pid_standard(float err, float prev_err, pid_gains gains, float freq)
{
    float u = gains.Kp*err + gains.Kd*(err-prev_err)*freq;
    return u;
}

float compute_position_pid_velocity(float err, float vel, pid_gains gains)
{
    float u = gains.Kp*err - gains.Kd*vel;
    return u;
}

void position_pid_task(void *pvParameters)
{
    ESP_LOGI(TAG_position_PID, "[%i] Entered position control setup", 0);
    //-------- SETUP
    ESP_LOGI(TAG_position_PID, "[%i] Setting up parameters...", 0);
    // compute the period of the control loop - once at runtime! so that we don't need to be constantly dividing
    Umax_inv = 1/Umax;
    float counts_to_radians = 2*PI / encoder_counts_per_rev; // output in radians
    // float radians_to_counts = 1/counts_to_radians;
    // float radians_to_degrees = 180/PI;
    // float degrees_to_radians = PI/180;

    // Setup control gains
    pid_gains pos_gains;
    pos_gains.Kp = Kp_pos;
    pos_gains.Kd = Kd_pos;
    pos_gains.Ki = Ki_pos;
    ESP_LOGI(TAG_position_PID, "[%i] Parameters:\nFrequency: %f\nEncoder Counts: %i\nKp: %f\nKd: %f\nKi: %f", 0, ctrl_freq_position, encoder_counts_per_rev, Kp_pos, Kd_pos, Ki_pos);


    // initial values
    float des_pos = 0.0; // the desired position of the motor
    float curr_pos = 0.0; // the measured position - always will be set to 0
    float curr_vel = 0.0; // the measured velocity - always will be set to 0
    float prev_pos = 0.0; // the previous measured position - always will start at 0
    // float prev_vel = 0.0;
    int curr_pos_enc_counts = 0; // the current encoder counts of the system

    // initial error values
    float err = 0.0; // the position error
    float prev_err = 0.0; // the position error

    // control parameters
    float  U = 0.0; // control output

    //-------- MAIN CONTROL LOOP
    TickType_t last_wake_time = xTaskGetTickCount(); // get the beginning time loop
    while (1) 
    {
        //-------- READ MEASUREMENT
        ctrl_loop_read(&curr_pos_enc_counts);

        //-------- UPDATE CONTROL WITH USER INPUT
        if(xSemaphoreTake(xMutex, 0))
        {
            des_pos = COMMAND_POS;
            xSemaphoreGive(xMutex);
        }

        curr_pos = curr_pos_enc_counts*counts_to_radians; // convert encoder counts to radians
        err = des_pos - curr_pos; //get the position error
        curr_vel = (curr_pos - prev_pos)*ctrl_freq_position; // computer the current velocity
        switch(mode) // switch based on the set PID mode
        {
            case STANDARD:
                U = compute_position_pid_standard(err, prev_err, pos_gains, ctrl_freq_position);
                break;
            case VELOCITY:
                U = compute_position_pid_velocity(err, curr_vel, pos_gains);
                break;
        }

        //-------- WRITE OUPUTS TO MOTOR DRIVER
        ctrl_loop_write(&U);

        // store data in the buffers
        if(xSemaphoreTake(xMutex, 0))
        {
            ACTUAL_POS = curr_pos;
            ENCODER_COUNTS = curr_pos_enc_counts;
            ERROR = err;
            CONTROL_SIGNAL = U;
            xSemaphoreGive(xMutex);
        }

        // Set the previous variables for our next loop
        prev_err = err;
        prev_pos = curr_pos;
        vTaskDelayUntil(&last_wake_time, pdMS_TO_TICKS(1));
    }
}

//-------- POTENTIOMETER FUNCTIONS
static bool IRAM_ATTR s_conv_done_cb(adc_continuous_handle_t handle, const adc_continuous_evt_data_t *edata, void *user_data)
{
    BaseType_t mustYield = pdFALSE;
    //Notify that ADC continuous driver has done enough number of conversions
    vTaskNotifyGiveFromISR(read_pot_task, &mustYield);

    return (mustYield == pdTRUE);
}

static void continuous_adc_init(adc_channel_t *channel, uint8_t channel_num, adc_continuous_handle_t *out_handle)
{
    adc_continuous_handle_t handle = NULL;

    adc_continuous_handle_cfg_t adc_config = {
        .max_store_buf_size = 1024,
        .conv_frame_size = EXAMPLE_READ_LEN,
    };
    ESP_ERROR_CHECK(adc_continuous_new_handle(&adc_config, &handle));

    adc_continuous_config_t dig_cfg = {
        .sample_freq_hz = 20 * 1000,
        .conv_mode = EXAMPLE_ADC_CONV_MODE,
    };

    adc_digi_pattern_config_t adc_pattern[SOC_ADC_PATT_LEN_MAX] = {0};
    dig_cfg.pattern_num = channel_num;
    for (int i = 0; i < channel_num; i++) {
        adc_pattern[i].atten = EXAMPLE_ADC_ATTEN;
        adc_pattern[i].channel = channel[i] & 0x7;
        adc_pattern[i].unit = EXAMPLE_ADC_UNIT;
        adc_pattern[i].bit_width = EXAMPLE_ADC_BIT_WIDTH;

        ESP_LOGI(TAG_pot, "adc_pattern[%d].atten is :%"PRIx8, i, adc_pattern[i].atten);
        ESP_LOGI(TAG_pot, "adc_pattern[%d].channel is :%"PRIx8, i, adc_pattern[i].channel);
        ESP_LOGI(TAG_pot, "adc_pattern[%d].unit is :%"PRIx8, i, adc_pattern[i].unit);
    }
    dig_cfg.adc_pattern = adc_pattern;
    ESP_ERROR_CHECK(adc_continuous_config(handle, &dig_cfg));

    *out_handle = handle;
}

void read_potentiometer_task(void *pvParameters)
{
    esp_err_t ret;
    uint32_t ret_num = 0;
    uint8_t result[EXAMPLE_READ_LEN] = {0};
    memset(result, 0xcc, EXAMPLE_READ_LEN);

    adc_continuous_handle_t handle = NULL;
    continuous_adc_init(channel, sizeof(channel) / sizeof(adc_channel_t), &handle);

    ESP_ERROR_CHECK(adc_continuous_start(handle));
    while (1) 
    {
        while (1) 
        {
            ret = adc_continuous_read(handle, result, EXAMPLE_READ_LEN, &ret_num, 0);
            if (ret == ESP_OK) {
                // ESP_LOGI("TASK", "ret is %x, ret_num is %"PRIu32" bytes", ret, ret_num);

                adc_continuous_data_t parsed_data[ret_num / SOC_ADC_DIGI_RESULT_BYTES];
                uint32_t num_parsed_samples = 0;

                esp_err_t parse_ret = adc_continuous_parse_data(handle, result, ret_num, parsed_data, &num_parsed_samples);
                if (parse_ret == ESP_OK) {
                    if (parsed_data[num_parsed_samples-1].valid) {
                        // ESP_LOGI(TAG_pot, "ADC%d, Channel: %d, Value: %"PRIu32,
                        //             parsed_data[num_parsed_samples-1].unit + 1,
                        //             parsed_data[num_parsed_samples-1].channel,
                        //             parsed_data[num_parsed_samples-1].raw_data);
                        // COMMAND_POS = ((float)(parsed_data[num_parsed_samples-1].raw_data)/2048.0 - 1)*2*PI;
                        if(xSemaphoreTake(xMutex, 0))
                        {
                            COMMAND_POS = ((float)(parsed_data[num_parsed_samples-1].raw_data)/2048.0 - 1)*PI;
                            POT_POSITION = parsed_data[num_parsed_samples-1].raw_data;
                            xSemaphoreGive(xMutex);
                        }
                        // ESP_LOGI(TAG_pot, "Pot Position: %i, Desired Position: %f", parsed_data[num_parsed_samples-1].raw_data, COMMAND_POS);
                    }
                }

                /**
                 * Because printing is slow, so every time you call `ulTaskNotifyTake`, it will immediately return.
                 * To avoid a task watchdog timeout, add a delay here. When you replace the way you process the data,
                 * usually you don't need this delay (as this task will block for a while).
                 */
                vTaskDelay(pdMS_TO_TICKS(10)); // run fast, if you can!
            }
            else if (ret == ESP_ERR_TIMEOUT)
            {
                //We try to read `EXAMPLE_READ_LEN` until API returns timeout, which means there's no available data
                break;
            }
        }
    }
    ESP_ERROR_CHECK(adc_continuous_stop(handle));
    ESP_ERROR_CHECK(adc_continuous_deinit(handle));
}

//-------- DISPLAY FUNCTIONS
void display_control_data_task(void *pvParameters)
{
    while(1)
    {
        if(xSemaphoreTake(xMutex, 0))
        {
            ESP_LOGI(TAG_display, "CONTROL DATA:\t\ndes_pos: %f,\ncurr_pos: %f,\npot_pos: %i,\nerr: %f,\nu(t): %f,\nenc_counts: %i\n\n", 
                    COMMAND_POS,
                    ACTUAL_POS,
                    POT_POSITION,
                    ERROR,
                    CONTROL_SIGNAL,
                    ENCODER_COUNTS);
            // return mutex
            xSemaphoreGive(xMutex);
        }
        // display data 10 times a second
        vTaskDelay(pdMS_TO_TICKS(100));
    }
}

//-------- MAIN
void app_main(void)
{
    // create da mutex
    xMutex = xSemaphoreCreateMutex();

    // setup the counter first
    ESP_LOGI(TAG_main, "[%i] Setting up pulse counter for quadrature decoder...", 0);
    setup_pcnt_stuff();

    // setup the PWM generator next
    ESP_LOGI(TAG_main, "[%i] Setting up PWM generator for control signal...", 0);
    setup_ledc_stuff();

    // setup GPIO pins
    ESP_LOGI(TAG_main, "[%i] Setting up GPIO pins for signal outputs...", 0);
    setup_gpio_stuff();

    // setup RTOS Tasks
    ESP_LOGI(TAG_main, "[%i] Setting up RTOS tasks...", 0);
    ESP_LOGI(TAG_main, "[%i] SETTING UP POSITION CONTROL TASK", 0);
    // priorities recommended from online, though I don't think the position task needs a priority lol
    xTaskCreatePinnedToCore(position_pid_task, "position_pid", 8192, NULL, 10, &control_loop_task, 1);
    ESP_LOGI(TAG_main, "[%i] SETTING UP POTENTIOMETER TASK", 0);
    xTaskCreatePinnedToCore(read_potentiometer_task, "poteniometer", 10000, NULL, 5, &read_pot_task, 0);
    ESP_LOGI(TAG_main, "[%i] SETTING UP DISPLAY TASK", 0);
    xTaskCreatePinnedToCore(display_control_data_task, "display", 8192, NULL, 1, &display_data_task, 0);
    return;
}
